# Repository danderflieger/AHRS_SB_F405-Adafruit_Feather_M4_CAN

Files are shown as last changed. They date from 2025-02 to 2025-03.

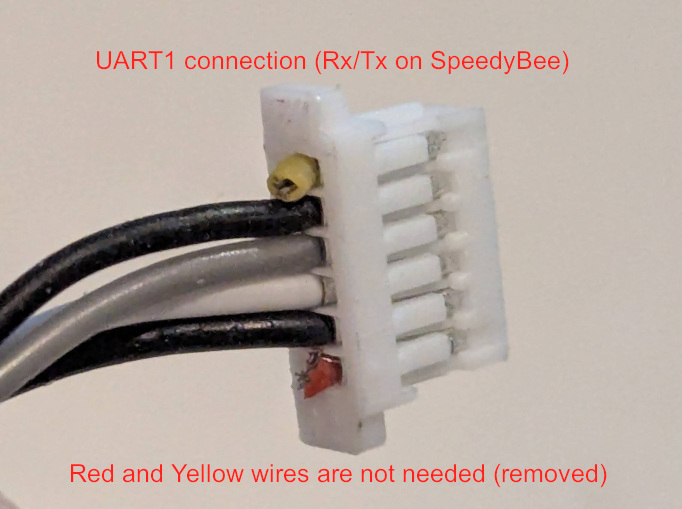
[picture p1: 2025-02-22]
Photos/PXL_20250222_135404890.jpg

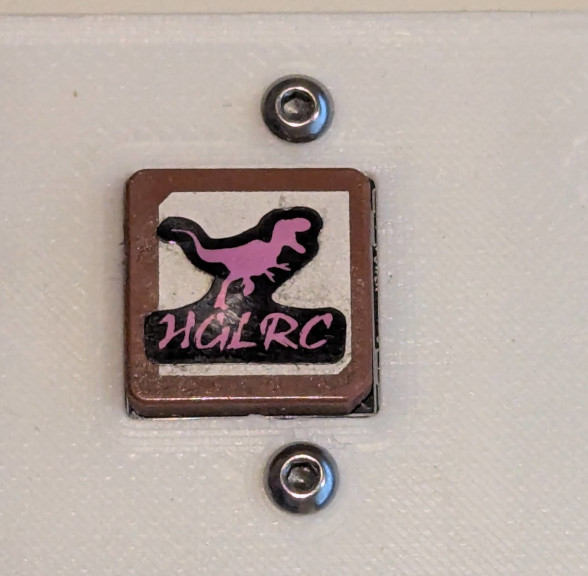
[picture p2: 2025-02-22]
Photos/PXL_20250222_134933491.jpg

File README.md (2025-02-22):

# *** FOR EXPERIMENTAL USE ONLY ***

# AHRS_SB_F405-Adafruit_CAN_Feather
Connects to a "Speedy Bee F405 Wing APP" radio controlled Airplane flight controller to collect AHRS data:  
[https://www.speedybee.com/speedybee-f405-wing-app-fixed-wing-flight-controller/](https://www.speedybee.com/speedybee-f405-wing-app-fixed-wing-flight-controller/)

The code is specifically for an "Adafruit Feather M4 CAN Express with ATSAME51" board, which has a built-in CAN transceiver and a beefy Cortex M4 chip:  
[https://www.adafruit.com/product/4759](https://www.adafruit.com/product/4759)

## Flight controller configuration
Some configuration needs to be done on the Speedy Bee. I used INAV Configurator version 7.1.2 to enable MAVLink on the UART1 port. 
I also have a MGLRC GPS (model: M100) connected to the Speedy Bee, which includes a magnetometer for magnetic heading. The GPS is enabled on UART3 under the Sensors column. See image below:



# Wiring
Ensure the buck converter is configured for 5V to 5.1V output or you will likely fry your boards.

The PCB carrier board lists the various connections that go into the terminal blocks, as well as the locations/orientations for the other boards that connect to it. 

There are six terminal block connections and the PCB lists what goes where:
- F405 Power
  - V+: I used a 90 degree USB-C power cable to plug into the SpeedyBee programming board. The positive wire goes here
  - GND: the negative USB-C power cable goes here to feed ground to the SpeedyBee
- 12V Input
  - V+: This is power that comes from my CAN Bus board (12 volts)
  - GND: this is ground that comes from the CAN Bus Board. I also connected the two black wires from the SpeedyBee's UART1 port (which I configured for MAVLINK data). These two black wires are used as a common ground between the two boards.
- F405 UART
  - Rx: Gray wire from the SpeedyBee UART1 port
  - Tx: White wire from the SpeedyBee UART1 port
 
## Electronics photos
PXL_20250222_134715603 MP
PXL_20250222_134739750 MP





# Arduino Code (loaded on Adafruit Feather M4 CAN Express board)
Start by following the Adafruit tutorial demonstrating how to configure the Arduino IDE for use with this board: 
[https://learn.adafruit.com/adafruit-feather-m4-can-express/arduino-can-examples](https://learn.adafruit.com/adafruit-feather-m4-can-express/arduino-can-examples)

The code is in C++, so you can safely skip the CircuitPython examples (unless you want to learn - in that case, go for it). Once you can program the board with some example code, go ahead and copy mine over.

## What to know about my code

There are 3 boolean values that can be set near the top of the code to determine what kinds of data you would like the Feather board to output:
```
/*************************************/
/******* Select output type **********/
bool OUTPUT_SERIAL  = true;  // Output for the Arduino IDE's Serial Monitor - good for debugging
bool OUTPUT_aEFIS   = false; // Output for my aEFIS Android app - connect the feather's USB port to an OTG cable on an Android
bool OUTPUT_CAN     = true;  // Output CAN data in MakerPlane CAN-FiX format 
/*************************************/
/*************************************/
```

Depending on which type of output you want, you will want to change these boolean values. For example, my aEFIS app is a simple attitude indicator that runs on an Android device. It uses the USB port on the Feather board to plug into the Android device for passing data and for powering the Feather board (e.g. the phone powers the Feather when plugged into the USB ports of both - the phone may require an OTG cable on its end, but most USB-C devices auto-negotiate). 

Because both the Arduino Serial Monitor (e.g. what you use to debug in the Arduino IDE) and aEFIS (e.g. my Android EFIS app) use the USB port on the Feather, you can't have both enabled at the same time or you will get wonky data. However, since the CAN transceiver on the Feather uses a separate set of wires for communication, one of the USB outputs can be used at the same time as the CAN interface. The code snipped above shows the latter (e.g. Serial output to the Arduino IDE and CAN output to a MakerPlane device).

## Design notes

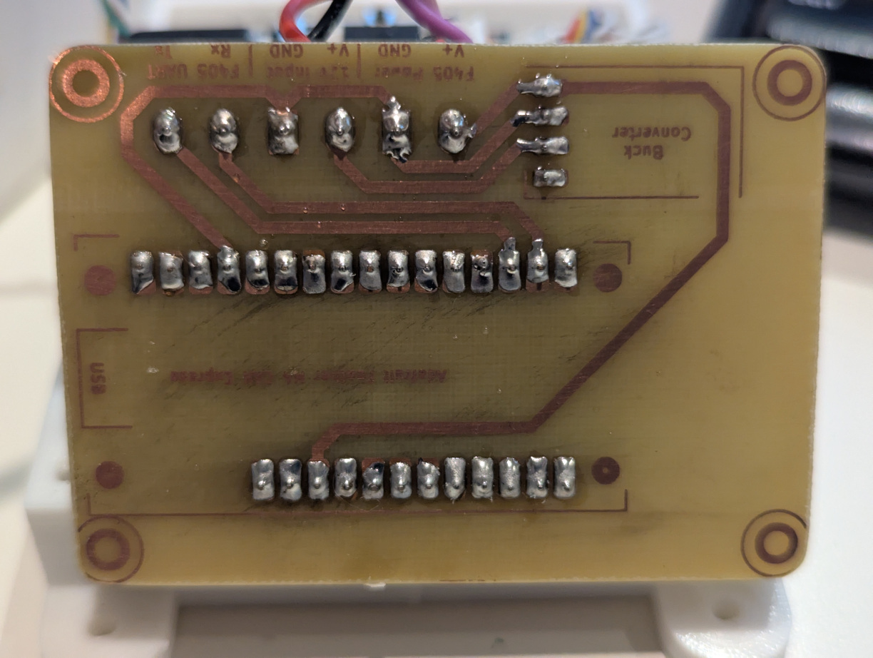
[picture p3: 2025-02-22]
Photos/PXL_20250222_134715603.MP.jpg

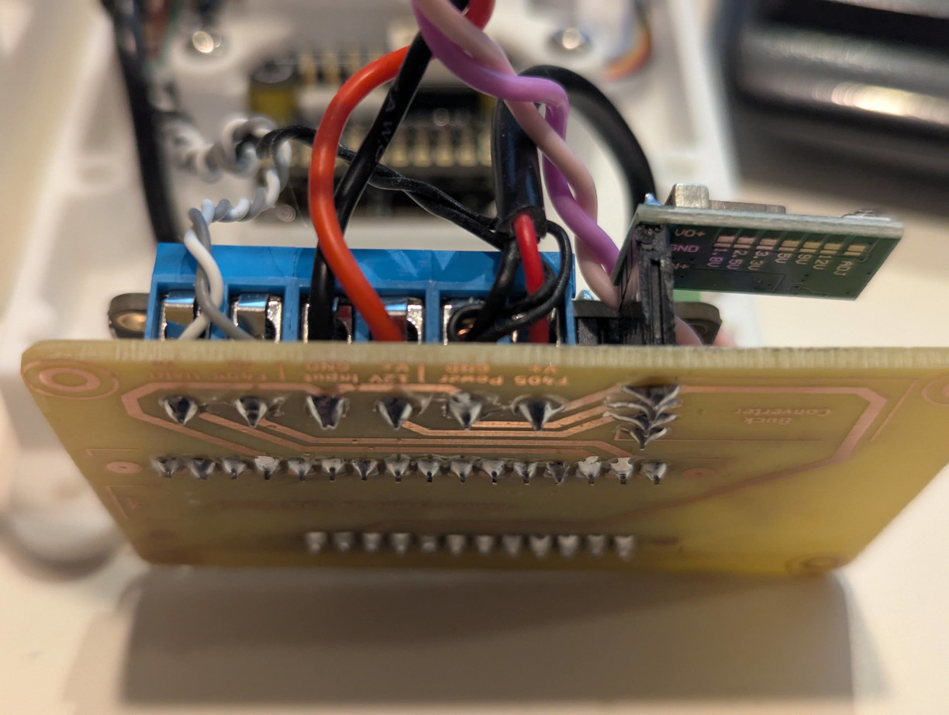
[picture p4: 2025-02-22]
Photos/PXL_20250222_134739750.MP.jpg

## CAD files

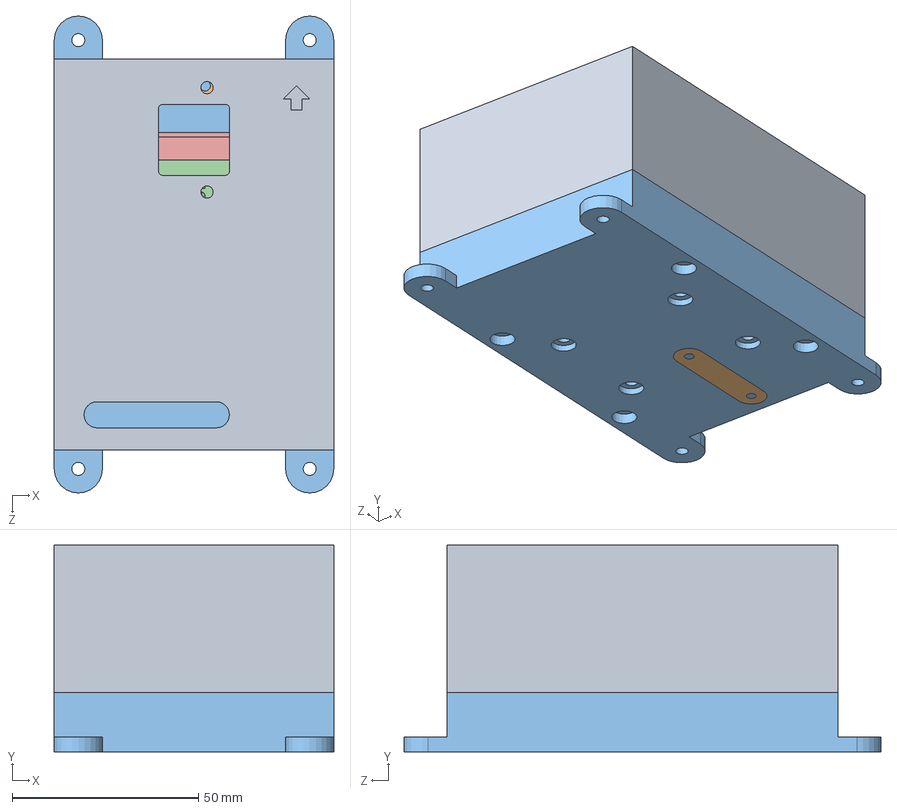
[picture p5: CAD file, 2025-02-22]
3D Models/Solidworks/Speedy_Bee_F450_Wing_Mount_Assembly.SLDASM
75.0 x 55.5 x 127.9 mm
Speedy_Bee_F450_Wing_Mount_Bottom
Speedy_Bee_F450_Wing_Mount_Top
Speedy_Bee_AHRS_Enclosure_Bottom
Enclusure_GPS_Lock
Speedy_Bee_AHRS_Enclosure_Top

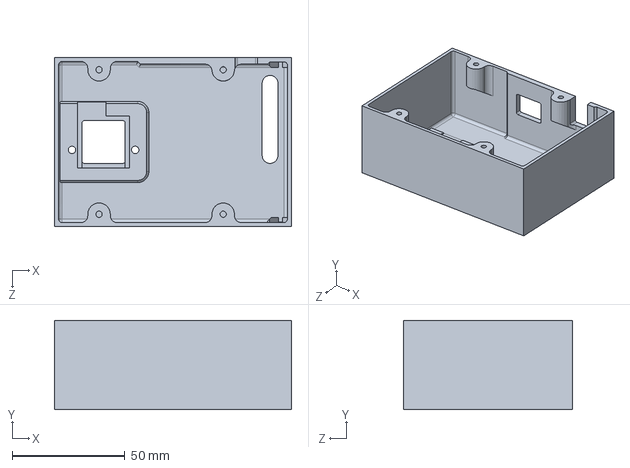
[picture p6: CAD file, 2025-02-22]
3D Models/Solidworks/Speedy_Bee_AHRS_Enclosure_Top.SLDPRT
105.0 x 39.5 x 75.0 mm

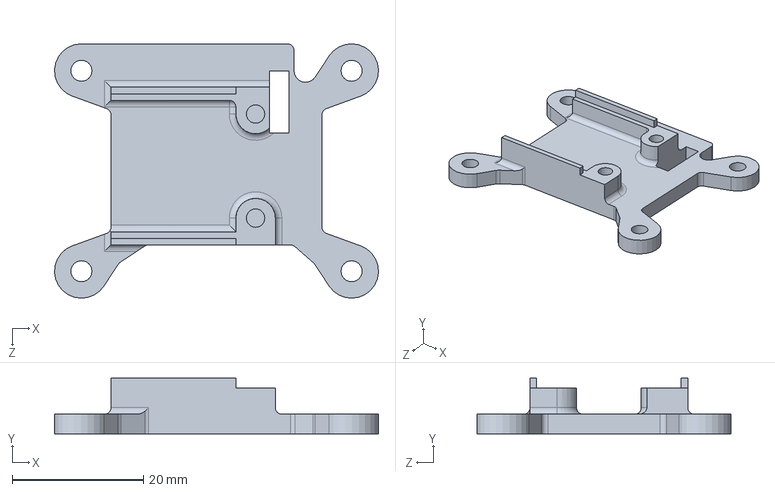
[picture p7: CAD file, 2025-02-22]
3D Models/Solidworks/Speedy_Bee_F450_Wing_Mount_Top.SLDPRT
49.3 x 8.50 x 38.7 mm

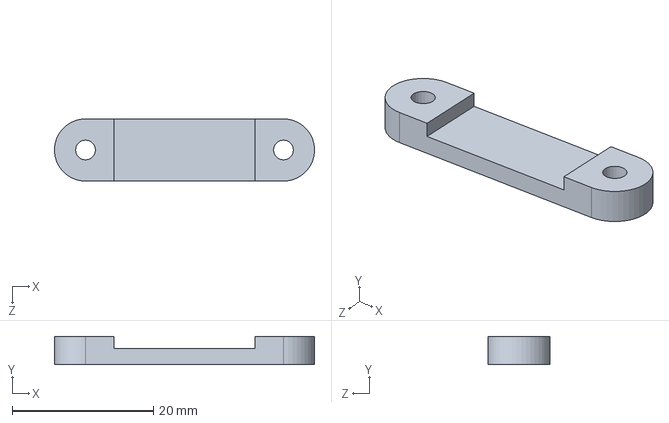
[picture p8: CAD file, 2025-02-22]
3D Models/Solidworks/Enclusure_GPS_Lock.SLDPRT
36.8 x 4.00 x 8.80 mm

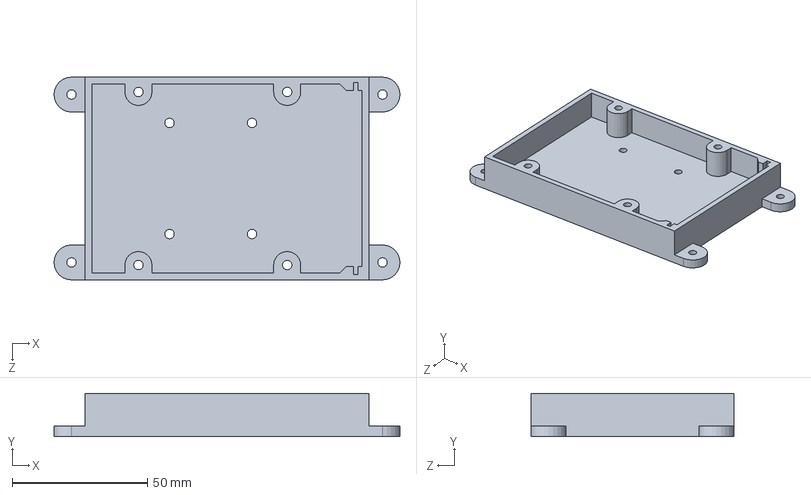
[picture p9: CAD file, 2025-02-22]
3D Models/Solidworks/Speedy_Bee_AHRS_Enclosure_Bottom.SLDPRT
127.9 x 16.0 x 75.0 mm

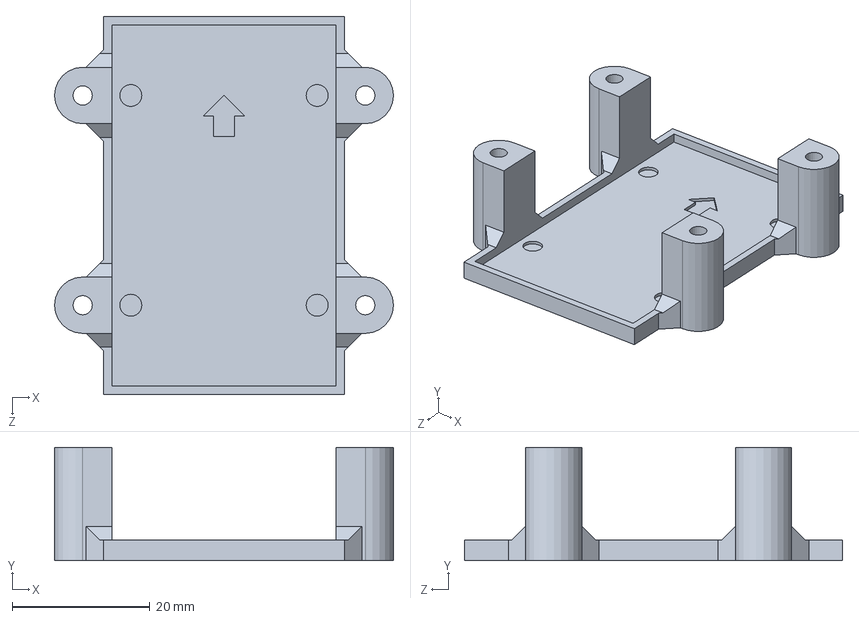
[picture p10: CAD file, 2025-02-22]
3D Models/Solidworks/Speedy_Bee_F450_Wing_Mount_Bottom.SLDPRT
49.3 x 16.5 x 55.0 mm

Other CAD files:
3D Models/STL/Enclusure_GPS_Lock.STL
3D Models/STL/Speedy_Bee_AHRS_Enclosure_Bottom.STL
3D Models/STL/Speedy_Bee_AHRS_Enclosure_Top.STL
3D Models/STL/Speedy_Bee_F450_Wing_Mount_Top.STL

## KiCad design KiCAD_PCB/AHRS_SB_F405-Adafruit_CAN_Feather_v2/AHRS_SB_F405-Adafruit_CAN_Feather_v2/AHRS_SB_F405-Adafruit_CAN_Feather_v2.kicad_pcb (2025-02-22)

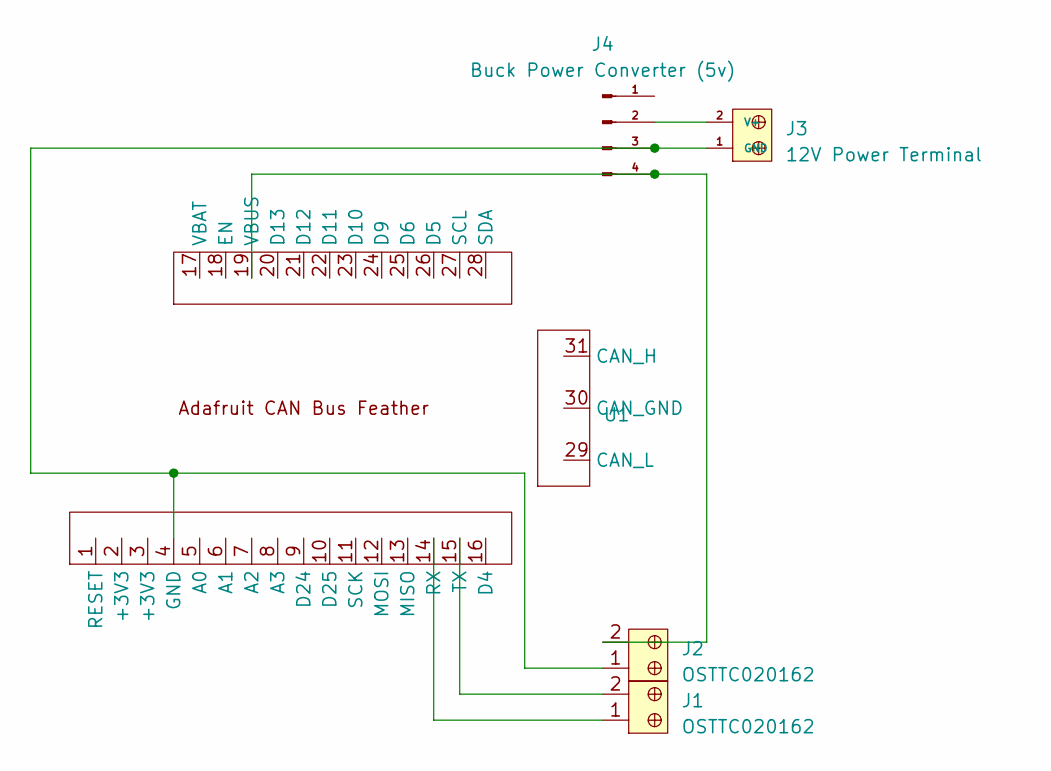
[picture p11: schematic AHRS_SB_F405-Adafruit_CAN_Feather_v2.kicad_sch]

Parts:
J1, J2: OSTTC020162; Term_Block_1x2_P5mm; MPN OSTTC020162; Digi-Key_PN ED2600-ND
J3: 12V Power Terminal; Term_Block_1x2_P5mm; MPN OSTTC020162; Digi-Key_PN ED2600-ND
J4: Buck Power Converter (5v); Buck_Converter
U1: Adafruit CAN Bus Feather

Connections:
unnamed: J2.1, J3.1 (GND), J4.3 (GND), U1.4 (GND)
unnamed: J3.2 (V+), J4.2 (VI)
unnamed: J2.2, J4.4 (VO_(5V)), U1.19 (VBUS)
unnamed: J1.1, U1.14 (RX)
unnamed: J1.2, U1.15 (TX)

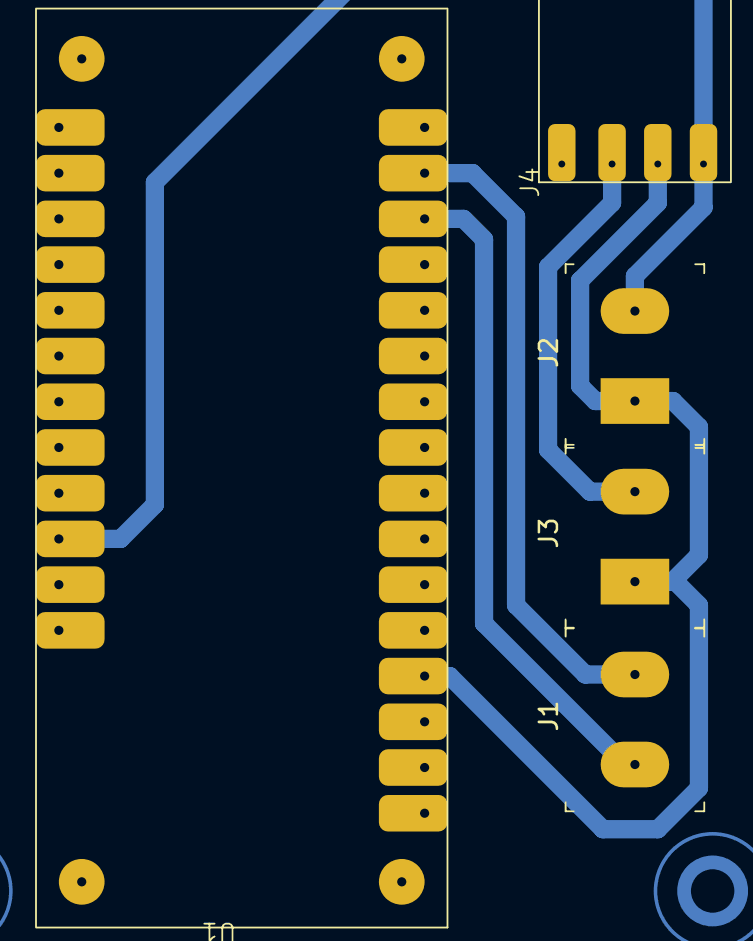
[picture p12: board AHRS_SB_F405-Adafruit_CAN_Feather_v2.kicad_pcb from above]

Board: 2 copper layers, 5 parts (0 on the bottom side), 5 nets.

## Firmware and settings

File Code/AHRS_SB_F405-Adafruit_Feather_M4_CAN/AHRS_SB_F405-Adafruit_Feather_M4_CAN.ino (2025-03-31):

#include <Arduino.h>
#include <MAVLink.h>
// #include <Adafruit_NeoPixel.h>

#include <CANSAME5x.h>
CANSAME5x CAN;

// Define serial port for MAVLink communication (Serial1 is available on RP2040)
#define MAVLINK_SERIAL Serial1

// MAVLink system and component IDs
#define MAVLINK_SYSTEM_ID 1   // This is the ID for this script
#define MAVLINK_COMPONENT_ID 1 // Component ID

// NeoPixel stuff
// #define LED_PIN 6
// #define LED_COUNT 1

// Adafruit_NeoPixel strip = Adafruit_NeoPixel(LED_COUNT, LED_PIN, NEO_GRB + NEO_KHZ800);

/*************************************/
/******* Select output type **********/
bool OUTPUT_SERIAL  = true;  // Output for the Arduino IDE's Serial Monitor - good for debugging
bool OUTPUT_aEFIS   = false; // Output for my aEFIS Android app - connect the feather's USB port to an OTG cable on an Android
bool OUTPUT_CAN     = true;  // Output CAN data in MakerPlane CAN-FiX format 
/*************************************/
/*************************************/


/******* MakerPlane CAN-FiX IDs ********/
// These values can be changed if you want to use another CAN standard
const uint16_t FIX_PITCH = 384;
const uint16_t FIX_ROLL = 385;
const uint16_t FIX_HEADING = 389;
// const uint16_t FIX_GROUND_SPEED = 453;
const uint16_t FIX_INDICATED_AIRSPEED = 387;
const uint16_t FIX_INDICATED_ALTITUDE = 388;

const uint16_t nodeId = 0x82;
/***************************************/


/**************************************/
// * Variables to store attitude data *
float roll = 0.0;
float pitch = 0.0;
float yaw = 0.0;
float ground_speed = 0.0;
float gps_altitude = 0.0;
int32_t global_heading = 0;

signed long lngPitch = 0;
signed long lngRoll = 0;
signed long lngGlobalHeading = 0;
unsigned long lngGroundSpeed = 0;
signed long lngGpsAltitude = 0;

/**************************************/


// Function to process incoming MAVLink messages
void handleMavlinkMessage() {
  mavlink_message_t msg;
  mavlink_status_t status;

  while (MAVLINK_SERIAL.available()) {
    uint8_t c = MAVLINK_SERIAL.read();

    if (mavlink_parse_char(MAVLINK_COMM_0, c, &msg, &status)) {
      // Message received, handle it
      switch (msg.msgid) {
        case MAVLINK_MSG_ID_ATTITUDE:
        {
          mavlink_attitude_t attitude;
          mavlink_msg_attitude_decode(&msg, &attitude);
          roll = attitude.roll;
          pitch = attitude.pitch;
          yaw = attitude.yaw;
          
          roll = roll * RAD_TO_DEG;
          pitch = pitch * RAD_TO_DEG;
          yaw = yaw * RAD_TO_DEG;
        
          break;
        }
        case MAVLINK_MSG_ID_GLOBAL_POSITION_INT:
        {
          mavlink_global_position_int_t global_position;
          mavlink_msg_global_position_int_decode(&msg, &global_position);
          // global_heading = global_position.hdg;
          // global_heading = global_heading / 10.0f;
          gps_altitude = (global_position.alt * 0.00328084);
          
          break;
        }
        case MAVLINK_MSG_ID_GPS_RAW_INT: {
          // Handle GPS_RAW_INT message (older MAVLink versions)
          mavlink_gps_raw_int_t gps_raw_int;
          mavlink_msg_gps_raw_int_decode(&msg, &gps_raw_int);
          ground_speed = gps_raw_int.vel;
          
          break;
        }
        default:
          // Ignore other messages or handle them as needed
          break;
      }

      lngPitch = pitch * 100;
      lngRoll = roll * 100;
      lngGlobalHeading = getHeadingReciprocal( yaw * 10 );
      lngGpsAltitude = gps_altitude;
      lngGroundSpeed = (ground_speed * 0.0194384) * 10;
      
      // long lngGlobalHeading = yaw * 10;

      if (OUTPUT_CAN) {
        sendCanMessage(FIX_PITCH, lngPitch);
        sendCanMessage(FIX_ROLL, lngRoll);
        sendCanMessage(FIX_HEADING, lngGlobalHeading);
        sendCanMessage(FIX_INDICATED_ALTITUDE, lngGpsAltitude);
        sendCanMessage(FIX_INDICATED_AIRSPEED, lngGroundSpeed);
      }

      if (OUTPUT_SERIAL) {
        Serial.print("pitch:"); Serial.print(lngPitch);
        Serial.print(",roll:"); Serial.print(lngRoll);
        Serial.print(",heading:");Serial.print(lngGlobalHeading);
        Serial.print(",altitude:");Serial.print(lngGpsAltitude);
        Serial.print(",speed:");Serial.println(lngGroundSpeed);

      }

      if (OUTPUT_aEFIS) {
        send_canfix_frame_to_aefis(FIX_PITCH, lngPitch);
        send_canfix_frame_to_aefis(FIX_ROLL, lngRoll);
        send_canfix_frame_to_aefis(FIX_HEADING, lngGlobalHeading);
        send_canfix_frame_to_aefis(FIX_INDICATED_ALTITUDE, lngGpsAltitude);
        send_canfix_frame_to_aefis(FIX_INDICATED_AIRSPEED, lngGroundSpeed);

      }
    }
  }
}

void sendCanMessage(int messageType, int data) {
  
  byte byteData[4];
  byteData[0] = data;
  byteData[1] = data >> 8;
  byteData[2] = data >> 16;
  byteData[3] = data >> 24;

  CAN.beginPacket(messageType);
  CAN.write(nodeId);
  CAN.write(0x00);
  CAN.write(0x00);
  for (int i = 0; i<4; i++) {
    CAN.write(byteData[i]);
  }

  CAN.endPacket();
  
}

// void send_canfix_frame_to_serial(CanFixFrame frame) {
void send_canfix_frame_to_aefis(int messageType, long data) {
  
  byte message [] = {
    messageType,
    messageType >> 8,
    messageType >> 16,
    0x78,//frame.data[0],
    0x00,//frame.data[1],
    0x00,//frame.data[2],
    data,
    data>>8,
    data>>16,
    data>>24

  };
  Serial.write(message, 11);
}

long getHeadingReciprocal(long heading) {
  // long reciprocal = (heading + 1800) % 3600;
  long reciprocal = (heading + 3600) % 3600;
  return reciprocal;
}


void setup() {
  
  Serial.begin(115200);
  
  // Prepare the USB port on the Adafruit board for use with either the
  // Arduino IDE or the aEFIS Android app, but not both.
  if (OUTPUT_SERIAL) {
    // For debugging on USB
    
    delay(1000);
    if (!Serial){
      // it's probably not starting, so don't try to send any messages over the Serial port anymore
      // OUTPUT_SERIAL = false;
    } else {
      Serial.println ("Serial Started ...");
    }
    delay(100);
  } else if (OUTPUT_aEFIS) {
    // For debugging on USB
    // Serial.begin(115200);
    delay(1000);
    while (!Serial) {
      delay(100);
    }
  }


  // Set up the connection from the Adafruit board to the Speedy Bee over Rx/Tx lines
  // Note: whichever UART port you're using on the Speedy Bee has to be configured to
  //        output MAVLink data or this entire project is basically useless
  MAVLINK_SERIAL.begin(115200); // MAVLink Serial Port Speed  (Commonly 57600 for Ardupilot)
  delay(100);
  if (!MAVLINK_SERIAL) {
    if (OUTPUT_SERIAL) {
      Serial.println("Error starting MAVLink ... continuing");
    }
  } else {
    if (OUTPUT_SERIAL) {
      Serial.println("MAVLink Attitude Listener Started");
    }
  }

  // From when I was playing around with NeoPixel stuff
  // strip.begin();  // initialize the strip
  // strip.show();   // make sure it is visible
  // strip.clear();  // Initialize all pixels to 'off'
  // strip.setPixelColor(0, 255, 0, 0);
  // strip.show();
  // delay(10);

  if (OUTPUT_CAN) {
    pinMode(PIN_CAN_STANDBY, OUTPUT);
    digitalWrite(PIN_CAN_STANDBY, false);
    pinMode(PIN_CAN_BOOSTEN, OUTPUT);
    digitalWrite(PIN_CAN_BOOSTEN, true);

    while (!CAN.begin(250000)) { // start the CAN bus at 250 kbps
      if (OUTPUT_SERIAL) {
        Serial.println("CAN failed to initialize! Will try again in 1 second ...");
        delay(1000);
      }
    }

    if (OUTPUT_SERIAL) {
      Serial.println("CAN started!");
    }

  }
  
  delay(500);
}


void loop() {
  handleMavlinkMessage();

  // More NeoPixel stuff
  // strip.setPixelColor(0, 255, 0, 0);
  // strip.show();
  // delay(10);

  //delay(3); //Small delay for loop rate
}

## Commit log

2024-12-26 Tried adding code to use the NeoPixel on the Adafruit board. Didn't work. Commented it out for now.
    [AHRS_SB_F405-Adafruit_Feather_M4_CAN.ino]
2024-12-31 Some debugging ... there was an issue where the code was hanging if there was no Serial connection. I wrote some code to disable the Serial connection if it's set to be in use, but doesn't connect. S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
    [AHRS_SB_F405-Adafruit_Feather_M4_CAN.ino]
2024-12-31 Change a couple of comments.
2024-12-31 Updated the getHeadingReciprocal() function. It was returning 180 degrees off. Fixed now.
    [AHRS_SB_F405-Adafruit_Feather_M4_CAN.ino]
2025-01-02 Added change in the code so that you can only either use Serial output or aEFIS output. They use the same USB port, but either strings or byte data so it doesn't make sense to support both at the sam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
    [AHRS_SB_F405-Adafruit_Feather_M4_CAN.ino]
2025-02-22 Added KiCAD files and moved the Arduino Code files into a directory called Code.
    [AHRS_SB_F405-Adafruit_CAN_Feather.kicad_pcb, AHRS_SB_F405-Adafruit_CAN_Feather.kicad_sch, AHRS_SB_F405-Adafruit_CAN_Feather_v2.kicad_pcb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]
2025-02-22 Added Solidworks 3D models and STL files
    [Enclusure_GPS_Lock.SLDPRT, Enclusure_GPS_Lock.STL, Speedy_Bee_AHRS_Enclosure_Bottom.SLDPRT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]
2025-03-28 Integrated/slightly modified some code by Ivan H's son Jon to add GPS Speed and GPS Altitude data.
    [CAN-FIX.ods]
2025-03-30 Reverted back to some older code that works - had some issues that I didn't realize when I checked in the last time.
    [AHRS_SB_F405-Adafruit_Feather_M4_CAN.ino]
2025-03-30 Fixed some code.
    [CAN-FIX.ods]
